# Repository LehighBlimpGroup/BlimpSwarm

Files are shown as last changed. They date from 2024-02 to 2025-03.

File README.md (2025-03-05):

# BLIMP SWARM
## [Click here for Documentation!](https://lehighblimpgroup.github.io/BlimpSwarm/)

BlimpSwarm is a framework to operate robots based on the ESP32 microcontroler.
### Please find [the indexed documentation here](https://github.com/LehighBlimpGroup/BlimpSwarm/blob/main/docs/index.md).

## FAQ

### Hardware

* Why does does only one servo or one motor not work, but the rest seem operational?
You likely have a loose/broken cable connection; If the cables are not broken (and need soldering or reinserting into the connecters), try just pushing the connectors together at every intersection. This can sometimes help the mechanical connecton to reoccur. 
If this does not solve your issue with one particular motor or servo, you might have a broken speed controller or a broken servo. Try using a test servo or test motor program to test these (or a servo tester if you have one). The motor itself can also break, and you can feel it by turining them by hand and observing the consistancy of the turning. The servo can be simalarly tested, but a servo is easier to break in this way. You can usually check if the servo is correcly powered by softly attempting to move them as they are powered and seeing if they want to move. One known issue is breaking servos due to insufficent current from the voltage booster. 

* Why does everything (motors and servos) turn on, but the robot doesnt seem to move up?
You likely have inverted motors or propellers. Make sure the propellers are correctly spinning in the correct direction and are pushing air down instead of up. If they are inverted, you need to switch any two wires in the connectors. You will need a sharp object to carefully lift the plastic blockers in the connecter to remove the wires and reinsert them in opposite positions (would recommend looking at a video).
Your robot might also be too heavy. 

* Why after I tried using all your troubleshooting tips, and I still cant solve the problem; I even used some methods you didnt mention and they failed!
There is a good chance the hardware on the PCB or the ESP32 failed. You may want to try replacing these to isolate the issue if possible to see if the issue still occurs. You may also be using an old version of the code, and may want to update the entire library to the github version. Sometimes the transeiver reduces in efficency from overuse, and the harware on the PCB can fail due to current spikes during operation. 

### Firmware

* The servos keep moving to weird positions when I start up, even though I set them to point up when the robot is in 'powered rest'. ( powered rest is the base setpoint of the servos when at rest, they should be pointing straight up).
This can be caused by the pitch feedback, try turning it off when trying. If you want pitch feedback and turining it off fixed this issue: set the pitch_offset parameter to 180 degrees from its current value. 

* Why does the flight work most of the time, but the turning while moving fowards seems very strange?
You likely have your servo1 connected to motor2 and vice versa. Check your hardware connections to make sure the front servo connection is on the same pair as the front motor connection. 

* Why does the pitch feedback fail force the servos to point straight up when it pitches, and go in the opposite direction?
Try setting inverting pitch_invert on the ground station from -1 to 1 or vice versa. 

* Why does my robot spin out of control when I start it up?
Try unplugging and replugging the blimp rapidly. Sometimes the capacitor causes the startup of the BNO to fail, and it will need a restart to correctly startup. 
Your yaw is likely inverted from the correct direction; try setting your kddyaw to negative or positive from its current direction. This is usally caused by the BNO being mounted upside down, but if that is required, you may need to edit the gains to accomidate for this. You can also double check by turining off yaw_en for yaw feedback, but your robot might unintentionally move in yaw due to the difference in servo angles when you first calibrate them. 

### Ground Station

* Why doesnt serial doesnt seem to be importing even though I did '$pip install pyserial'?: 
Your text editor is likely using a different version of python than the one you installed pyserial to: check to make sure these match or install pyserial to the installation of python used by your terminal/text editor.

* Why do I keep getting messages like "could not open port" when I run the ground station code?:
There are several reasons this could occur. 
#1 Make sure that your transiever code contains the correct 'BaseTranseiver.ino' code. 
#2 Make sure that your transiever arduino is connected to your computer, and check its port matches the one in 'user_parameters.py'.
#3 Make sure that the serial monitor of the transiever arduino is closed/not occupied by another process.

* Why isn't my blimp moving even though I turned the prorgram on?
#1 Make sure the robot is turned on.
    #a Make sure that you are sending an 'on' command in the python program (most use 'B' on the controller to start).
#2 Make sure the mac address in 'user_parameters.py' matches the mac address on the blimp.
#3 Make sure the robot code is correct: one of the bicopter.ino files ex: 'MultiRobotBicopter.ino'.
#4 Make sure the battery is charged (using a battery checker or at minimum, you hear the ESCs arm when you plug the battery in).
#5 Make sure the motors are calibrated, as the calibration might result in not seeing the motors move. 
#6 If the above fail, you can follow the following debugging procedures to isolate the issue:
#a Plug in the serial cable to the robot and observe the serial monitor:
    If the serial monitor is not printing statements that have to do with the start of a robot, or sensor measurements; you likely have the wrong firmware.
    If the serial montior is working as normal, continue.
#b Check the mac address of the robot and match it to the one in 'user_parameters.py'.
    If they are different, change and test again.
#c While observing the serial monitor, turn on the ground station code. You should see commands being recieved by the blimp on the serial monitor. (this will require two USB ports and cables) (You should not have the battery plugged into the blimp for this, unless you want to see the motors turn on while observing the serial monitor.)
    If you see nothing, you likely have some transmitter/reciever issues, but I would double check the firmware on the transeiver code, and the mac and ports are matching up on 'user_parameters.py'.
    If you see commands being recieved, you likely have a working robot, but if it still doesnt work, I would check to make sure the battery is OK and that the cables are connected correctly. Mismatches in the wiring could cause no movement even when commands are being received.

### Nicla Vision

* If you are not getting feedback from your niclavison on your arduino, you may try some of the following steps:
#1 double check that the nicla has the correct code, and it is properly downloaded on board as 'main.py'.
#2 connect the Serial monitor of your ESP32 on the blimp to the computer and make sure the nicla is powered and connected to the ESP32. Check to see if the serial monitor is getting values in the sensor measurements of the nicla (values 11-20) and that they are not crazy large values that occur when the nicla has not started up yet.
#3 double check that the nicla is properly powered, or directly connect it to your computer with a cable (will require 2 USB ports and cables)
    If you are sure that your nicla is seeing things and sending values, and you do not see anything on the ESP32 side even thought they are connected, you could have a broken Nicla vison or Nicla vision PCB. Check both by replacing them one at a time to see which is actually broken. The ESP32 PCB might also be broken but it is less likely.

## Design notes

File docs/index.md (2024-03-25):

---
title: Home
---

## BlimpSwarm Framework: Tutorials and Documentation





* [Bicopter robot: Parts and assembly](bicopter)
* [Firmware: Install and test](bicopter/firmware.md)
* [Computer Vision: Install and test](bicopter/vision.md)

More information about our team: [Swarms Lab Club](https://swarmslab.com/club/)

<iframe width="560" height="315" src="https://www.youtube.com/embed/4HuQvzdmefU?si=GS-7wAQmuWwk3HFo" title="YouTube video player" frameborder="0" allow="accelerometer; autoplay; clipboard-write; encrypted-media; gyroscope; picture-in-picture; web-share" allowfullscreen></iframe>

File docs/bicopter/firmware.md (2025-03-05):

---
title: Firmware: How to start
---

# Firmware: How to start

## 0. Before starting
Follow the instructions to assemble the robot [here](https://rhinestone-star-fa9.notion.site/Robot-Assembly-f31e5685cc46427f9f4b832dc4a56b95). Do not install the propellers.

The main board is a customized PCB that integrates the power management for the ESP32 and for the servo motors, the power outlet to the brushless ESC, the communication outlet with the vision board, and the I2C bus for the sensors.
View the PCB print of [the top layer here](https://github.com/LehighBlimpGroup/BlimpSwarm/blob/main/docs/figs/esp_board_front.pdf), and [the bottom layer here](https://github.com/LehighBlimpGroup/BlimpSwarm/blob/main/docs/figs/esp_board_back.pdf). We also provide the [Fusion 360 Electronics archive](https://github.com/LehighBlimpGroup/BlimpSwarm/blob/main/docs/figs/Blimp_ESP_board_standalone_IC_power.f3z), [the board design](https://github.com/LehighBlimpGroup/BlimpSwarm/blob/main/docs/figs/Blimp_ESP_board_standalone_IC_power.brd), [the scheme](https://github.com/LehighBlimpGroup/BlimpSwarm/blob/main/docs/figs/Blimp_ESP_board_standalone_IC_power.sch), and the [Assembly Files here](https://github.com/LehighBlimpGroup/BlimpSwarm/blob/main/docs/figs/Blimp_ESP_board_standalone_IC_power%20v94_2024-10-04.zip).

## 1. Install the robot firmware
For this part, you must have two ESP32 microchips (one with pins and one without pins). The setup looks like the following fitgure
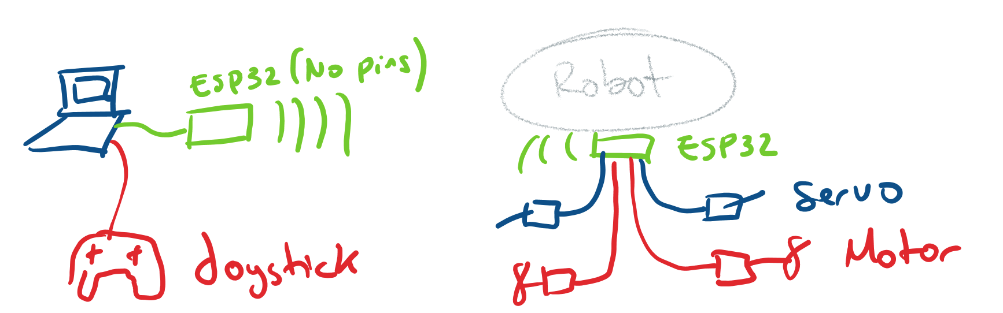
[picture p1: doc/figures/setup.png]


 Follow the following steps to install the firmware on both microchips:
1. Install [Arduino IDE 2.3.0](https://www.arduino.cc/en/software) or latest on your computer.
2. Download [BlimpSwarm](https://github.com/LehighBlimpGroup/BlimpSwarm) into the Arduino/libraries folder.
3. In Arduino open the menu ```File->Examples->BlimpSwarm->Bicopter1raw```.
4. Connect the ESP32 (with pins) to your computer through USB. 
   * Select the device XIAO_ESP32S3
   * Select the port of the ESP32. E.g., COM1 in Windows, /dev/ttyACM0 in Linux, or /dev/tty.usbmodem14301 in MacOS.
5. Click on Upload
6. Click on serial Monitor, and copy the MAC address (e.g., 34:85:18:AC:BB:70). Then, close the Serial Monitor.
7. Disconnect your ESP32 and Repeat the same process to install ```File->Examples->BlimpSwarm->BaseTranseiver``` in the ESP32 (without pinS). That is the ESP32 that will be connected to your computer and act as a radio communicator.

## 2. Control the actuators (servos and motors using the Joystick)

1. Connect the Joystick to the computer
2. Edit the Python file BlimpSwarm/swarmbase/RawBicopterJoystick.py
```
    Update the ROBOT_MAC of your robot
    Update the port of the ESP32 (same as the one in Arduino)
```
3. Run the file ```RawBicopter.py```. 
4. Move the left vertical joystick. 
   * The LED in your ESP32 should turn on when you move the vertical joystick

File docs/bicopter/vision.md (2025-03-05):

---
title: Computer Vision
---

# Vision Module

## Hardware Requirements
For this tutorial, you need the _Arduino Nicla Vision_ and the _Vision Module_.
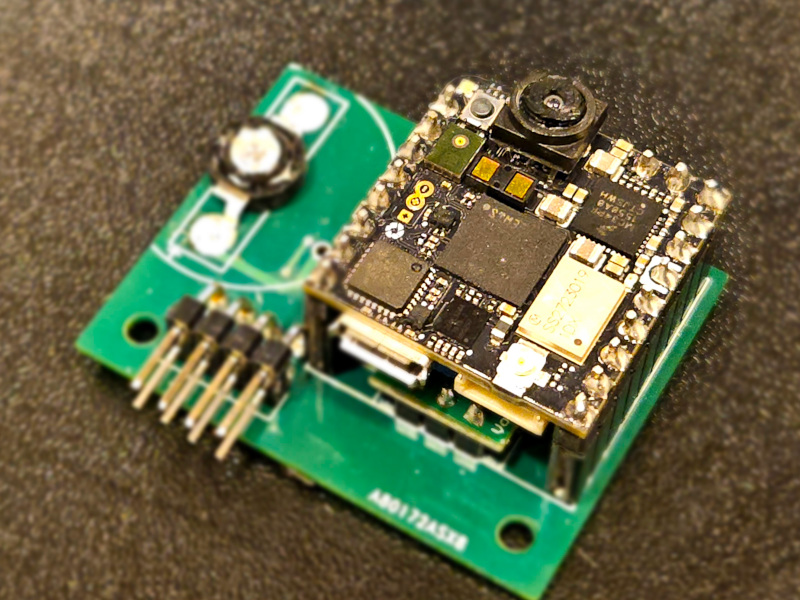
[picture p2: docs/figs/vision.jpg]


The Vision Module is a customized PCB that integrates the power management, the communication outlet with the main ESP board, and a power LED driver.
View the PCB print of [the top layer here](https://github.com/LehighBlimpGroup/BlimpSwarm/blob/main/docs/figs/nicla_board_front.pdf), and [the bottom layer here](https://github.com/LehighBlimpGroup/BlimpSwarm/blob/main/docs/figs/nicla_board_back.pdf). We also provide the [Fusion 360 Electronics archive](https://github.com/LehighBlimpGroup/BlimpSwarm/blob/main/docs/figs/Blimp_nicla_standalone_IC.f3z), [the board design](https://github.com/LehighBlimpGroup/BlimpSwarm/blob/main/docs/figs/Blimp_nicla_standalone_IC.brd), [the scheme](https://github.com/LehighBlimpGroup/BlimpSwarm/blob/main/docs/figs/Blimp_nicla_standalone_IC.sch), and the [Assembly Files here](https://github.com/LehighBlimpGroup/BlimpSwarm/blob/main/docs/figs/Blimp_nicla_standalone%20v57_2024-03-01.zip).

## Installation
1. Install _OpenMV IDE v4.1.5_ or latest from [here](https://openmv.io/pages/download)
2. Download/Clone the Gihub repository [Blob-Detection-and-Tracking](https://github.com/LehighBlimpGroup/Blob-detection-and-Tracking/blob/main/Blob%20Detection.py)

# Blob-detection-and-Tracking
Blob detection, tracking and serial communication to esp32 through IBus protocol using an OpenMV compatible edge camera device. Currently it has two modes:
1. Pure color-based blob detection and tracking, which requires a fine-tuned threshold in LAB space. Look at [OpenMV documentation on the function find_blobs](https://docs.openmv.io/library/omv.image.html#image.Image.find_blobs) for detailed reference.
2. IR blinking-based detection for retro-reflective surfaces using a IR-filter-free lens. The camera captures two consecutive images with LED off and on, respectively, then compute pixel-wise difference to highlight the reflective surfaces in the environment. Refer to [the initial tests on the reflective solution for more details](https://github.com/LehighBlimpGroup/Reflective_AimBot).
    1. Under colored mode (`isColored = True`), the algorithm distinguishes the reflective surfaces with different colors.
    2. Under grayscale mode (`isColored = False`), the algorithm does not distinguish the reflective surfaces with different colors.

Both modes use the same moving-window-based tracking methods (see classes `Tracking_ROI` and `TrackedBlob`).

## The logic flow of ROI tracking:
1. Initialize the ROI as the maximum size of the image.
2. Whenever a new detection is fed, find its bounding box.
3. New ROI is a weight average of the current rectangular ROI and the detection bounding box.

## The logic flow of the blob tracking:
1. Initialization:
    1. find a reference blob by constraining the minimum roundness, density, and of course color
    2. initialize a feature vector and a history list of blobs based on the reference
        1. *feature vector*: a vector of {five} values marking the **average** center x, y position, width, height, and blob direction of the tracked blob history
        2. *history*: a list of blobs that the algorithm considers as the same blob through multiple frames
2. Update: check the feature vector of the tracked blob against new detected blobs in terms of 1-norm/2-norm feature vector distance
    1. if the history list is full, pop the oldest, push the latest. Otherwise populate it.
    2. if the new blob feature vector is too far from the tracked blob, mark the tracked blob with an additional missed track
    3. if the tracked blob has too many missed tracks, reset the tracked blob history and feature vector, then go to step 1.ii.

## The logic flow of the retro-reflective detection:
1. IR LED off, take image1.
2. IR LED on (~2W power LEDs), take image2.
3. Compute pixel-wise difference between image1 and image2 by `diff = image2 - image1`.
4. (Optional) Filter out differences due to motion by finding high-frequency edges on image1 and use them as a `mask`.
5. Negate `diff` to recover the original color of the reflective surfaces.
6. Find colored blobs on `diff` with regions marked with `mask` masked out.

## Parameters
1. `thresholds`: it determines the color to detect and track
2. In function `find_reference`, `density_threshold` and `roundness_threshold=0.4`: they determine how strictly dense and round the initial blob needs to be.
3. In initialization of the `TrackedBlob` object currently in function `find_reference`,
    1. `norm_level` controls the distance type, 1-norm is faster and 2-norm is smoother (try both and feel the difference)
    2. `feature_dist_threshold` controls how strict a feature vector match needs to be
    3. `window_size` controls how long a history of tracked blobs the user wants to keep. Higher value gives a smoother but more draggy track
4. If the nicla is connected to another device through uart, when it receives `0x80`, it will try to switch to balloon tracking mode. When it receives `0x81`,
   it will try to switch to goal tracking mode.
5. In the initialization of `Tracking_ROI` objects, `forgetting_factor` controls how rapid the bounding box is updated with respect to a new input or a new misinput.

## Pending:
1. `id`: we would like to identify/distinguish different blobs.

## `Thresholds.txt`
We recorded the (manually-tuned) optimal color thresholds for balloon detection under different initial and ambient lighting consitions in this file.

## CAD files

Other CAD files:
docs/figs/Blimp_ESP_board_standalone_IC_power.f3z
docs/figs/Blimp_nicla_standalone_IC.f3z

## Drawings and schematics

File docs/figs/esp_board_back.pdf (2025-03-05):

I2C xZ LR | RL

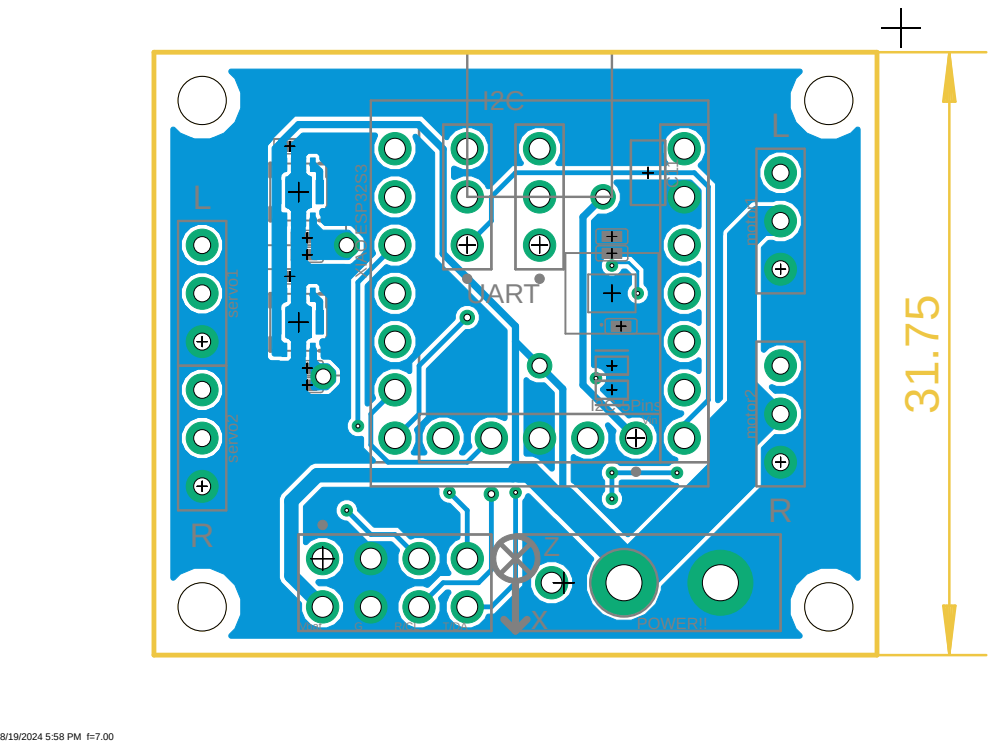
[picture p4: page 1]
Vbat; motor1 motor2 servo1 servo2; UART; I2C-5Pins; POWER!! C¹¹

Vin XIAO ESP³²S³

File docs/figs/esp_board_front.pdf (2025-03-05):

I2C
L

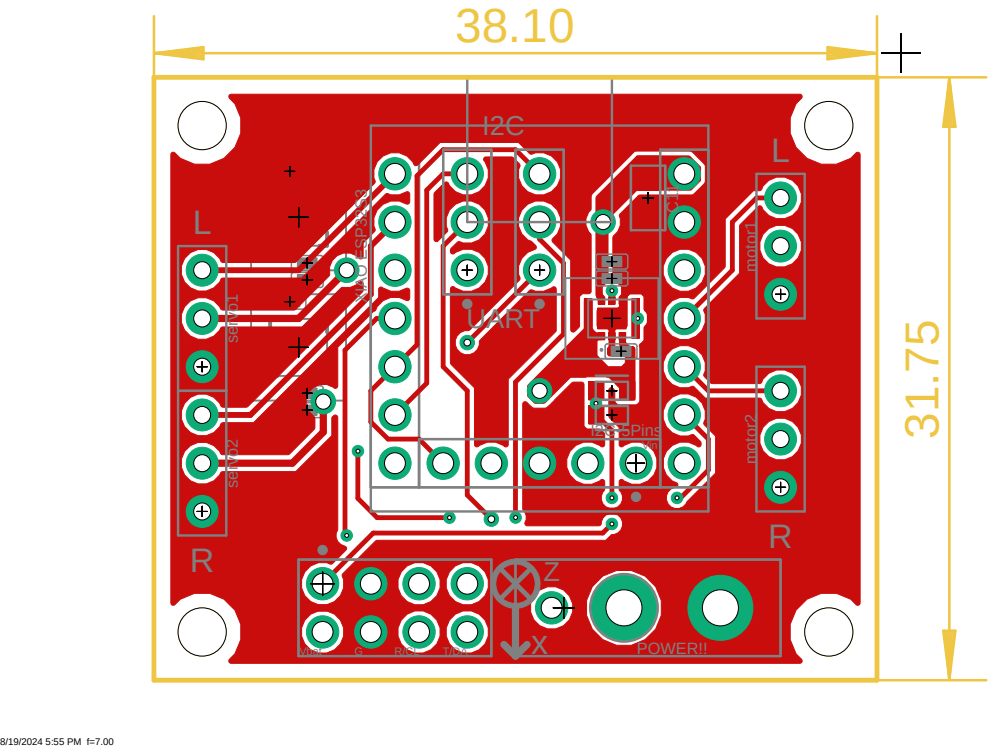
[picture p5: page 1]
Vbat; motor1 motor2 servo1 servo2; UART; I2C-5Pins; POWER!! C¹¹

Vin XIAO ESP³²S³

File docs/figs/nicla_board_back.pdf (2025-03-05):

40.64 31.75

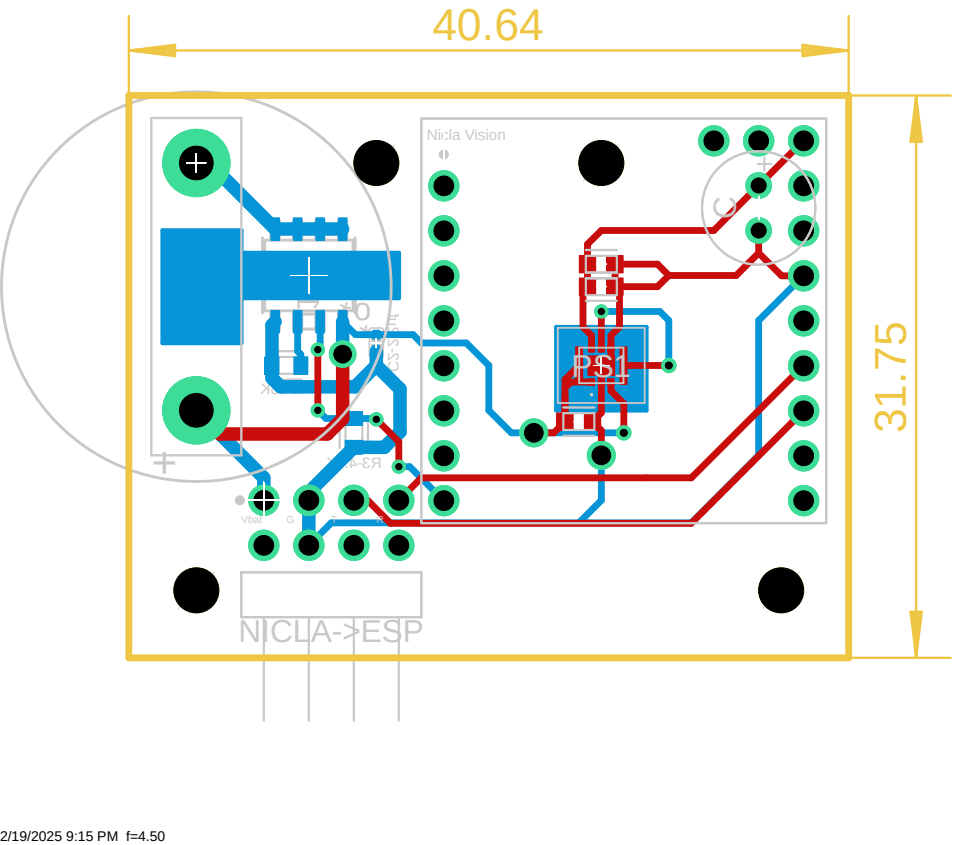
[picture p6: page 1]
Vbat; Nicla Vision; NICLA->ESP

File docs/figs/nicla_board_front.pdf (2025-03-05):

40.64 31.75

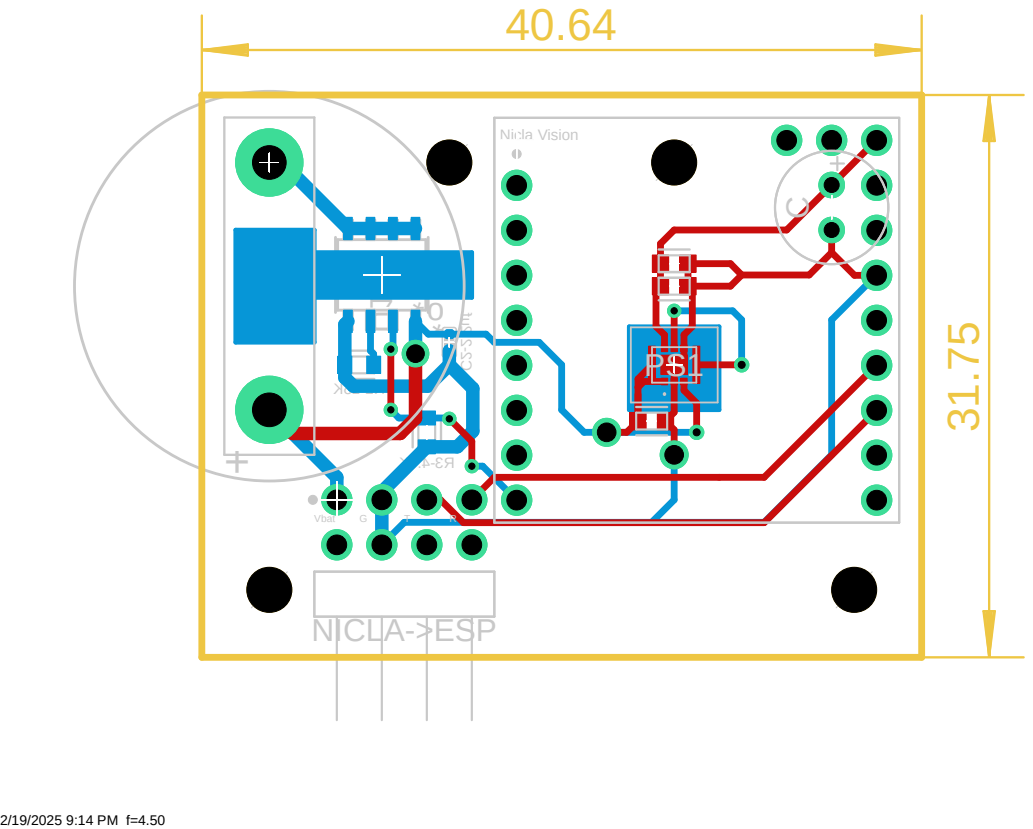
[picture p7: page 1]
Vbat; Nicla Vision; NICLA->ESP

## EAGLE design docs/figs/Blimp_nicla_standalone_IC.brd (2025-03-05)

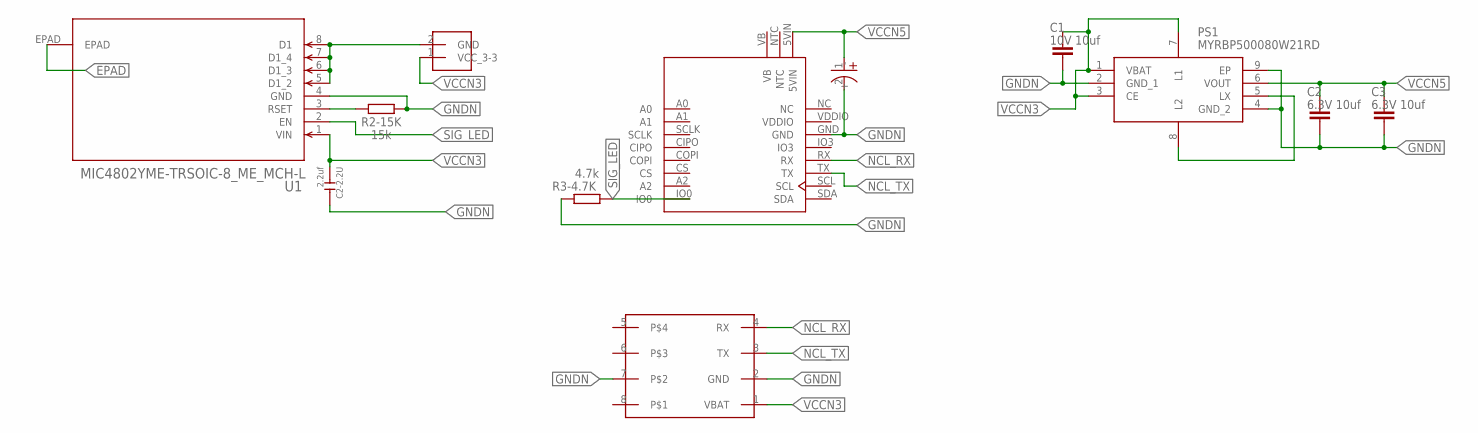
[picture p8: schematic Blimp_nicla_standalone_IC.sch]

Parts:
C1: 10V 10uf; CAPC1608X85
C2, C3: 6.3V 10uf; CAPC1608X85
C2-2.2U: 2.2uf; C0402
IR_LED1: UV_LIGHT
PS1: MYRBP500080W21RD
R2-15K: 15k; RESC1608X60
R3-4.7K: 4.7k; RESC1608X60
U1: MIC4802YME-TRSOIC-8_ME_MCH-L; SOIC-8_ME_MCH-L
U$6: NICLA_ESP_4PIN_CONNECTOR_MALE_ON_NICLA; ESP_NICLA_4X2PIN_CONNECTOR_MALE_ON_NICLA
U$9: CUSTOM_C; CAP
U$15: NICLAVISION; NICLA_FULL

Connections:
EPAD: U1.EPAD
GNDN: C1.2, C2.2, C2-2.2U.2, C3.2, PS1.2 (GND_1), PS1.4 (GND_2), PS1.9 (EP), R2-15K.2, R3-4.7K.2, U1.4 (GND), U$6.2 (GND), U$6.7, U$9.2 (-), U$15.GND
unnamed: IR_LED1.2 (GND), U1.5 (D1_2), U1.6 (D1_3), U1.7 (D1_4), U1.8 (D1)
unnamed: R2-15K.1, U1.3 (RSET)
unnamed: PS1.5 (LX), PS1.8 (L2)
NCL_RX: U$6.4 (RX), U$15.RX
NCL_TX: U$6.3 (TX), U$15.TX
SIG_LED: R3-4.7K.1, U1.2 (EN), U$15.IO0
VB: U$15.VB
VCCN3: C1.1, C2-2.2U.1, IR_LED1.1 (VCC_3-3), PS1.1 (VBAT), PS1.3 (CE), PS1.7 (L1), U1.1 (VIN), U$6.1 (VBAT)
VCCN5: C2.1, C3.1, PS1.6 (VOUT), U$9.1 (+), U$15.5VIN
VDDIO: U$15.VDDIO

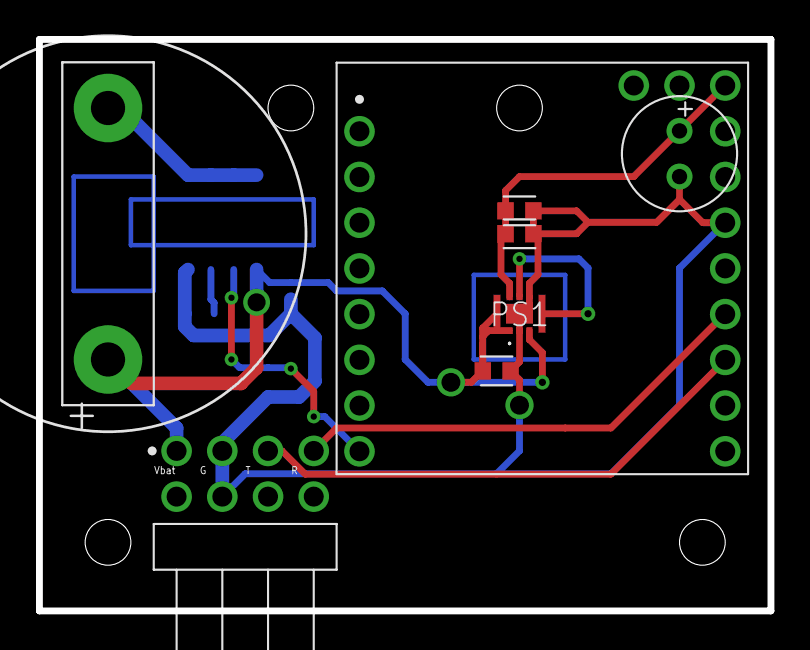
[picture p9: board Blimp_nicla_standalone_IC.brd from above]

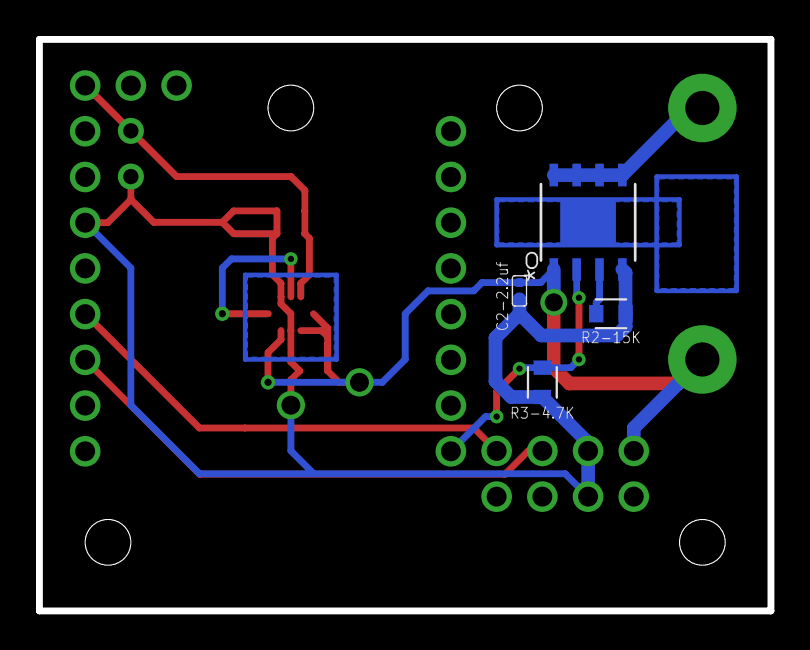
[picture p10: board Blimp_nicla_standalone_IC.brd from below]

Board: 2 copper layers, 40.6 x 31.8 mm, 12 parts (4 on the bottom side), 9 nets.

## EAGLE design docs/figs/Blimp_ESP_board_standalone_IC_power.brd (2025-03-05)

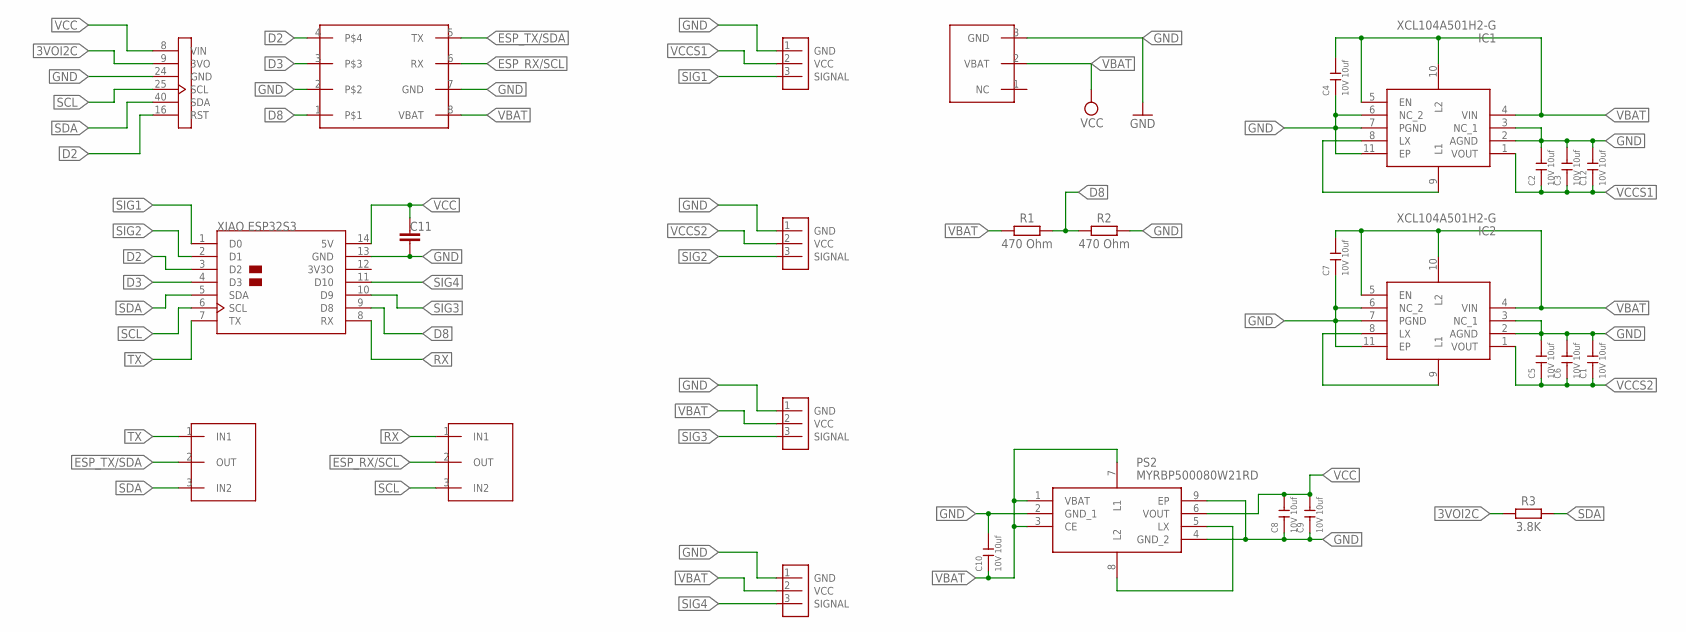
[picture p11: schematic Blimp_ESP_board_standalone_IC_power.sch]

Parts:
ACT1, ACT2, ACT3, ACT4: ESC; ESC_CONECTOR_FOOT
C1, C2, C3, C4, C5, C6, C7, C8, C9, C10, C12: 10V 10uf; C0402
C11: C_TANTALUM-1206(3216-METRIC); CAPM3216X180
IC1, IC2: XCL104A501H2-G; DFN3030-10B
PS2: MYRBP500080W21RD
R1, R2: 470 Ohm; RESC1608X60
R3: 3.8K; RESC1608X60
U1: XIAOESP32S3
U$1: BATTERY_CONNECTOR; 3PIN_CONNECTOR_FEMALE
U$2: I2C_6PIN_WRST
U$4, U$5: 3X1SELECTOR
U$7: NICLA_ESP_4PIN_CONNECTOR_FEMALE_ON_ESP; ESP_NICLA_4X2PIN_CONNECTOR_FEMALE_ON_ESP

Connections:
3VOI2C: R3.1, U$2.9 (3VO)
D2: U1.3 (D2), U$2.16 (RST), U$7.4
D3: U1.4 (D3), U$7.3
D8: R1.2, R2.1, U1.9 (D8), U$7.1
ESP_RX/SCL: U$5.2 (OUT), U$7.6 (RX)
ESP_TX/SDA: U$4.2 (OUT), U$7.5 (TX)
GND: ACT1.1 (GND), ACT2.1 (GND), ACT3.1 (GND), ACT4.1 (GND), C1.2, C2.2, C3.2, C4.1, C5.2, C6.2, C7.1, C8.1, C9.1, C10.2, C11.2, C12.2, IC1.2 (AGND), IC1.3 (NC_1), IC1.6 (NC_2), IC1.7 (PGND), IC1.11 (EP), IC2.2 (AGND), IC2.3 (NC_1), IC2.6 (NC_2), IC2.7 (PGND), IC2.11 (EP), PS2.2 (GND_1), PS2.4 (GND_2), PS2.9 (EP), R2.2, U1.13 (GND), U$1.3 (GND), U$2.24 (GND), U$7.2, U$7.7 (GND)
unnamed: IC1.8 (LX), IC1.9 (L1)
unnamed: IC2.8 (LX), IC2.9 (L1)
unnamed: PS2.5 (LX), PS2.8 (L2)
RX: U1.8 (RX), U$5.1 (IN1)
SCL: U1.6 (SCL), U$2.25 (SCL), U$5.3 (IN2)
SDA: R3.2, U1.5 (SDA), U$2.40 (SDA), U$4.3 (IN2)
SIG1: ACT3.3 (SIGNAL), U1.1 (D0)
SIG2: ACT2.3 (SIGNAL), U1.2 (D1)
SIG3: ACT1.3 (SIGNAL), U1.10 (D9)
SIG4: ACT4.3 (SIGNAL), U1.11 (D10)
TX: U1.7 (TX), U$4.1 (IN1)
VBAT: ACT1.2 (VCC), ACT4.2 (VCC), C4.2, C7.2, C10.1, IC1.4 (VIN), IC1.5 (EN), IC1.10 (L2), IC2.4 (VIN), IC2.5 (EN), IC2.10 (L2), PS2.1 (VBAT), PS2.3 (CE), PS2.7 (L1), R1.1, U$1.2 (VBAT), U$7.8 (VBAT)
VCC: C8.2, C9.2, C11.1, PS2.6 (VOUT), U1.14 (5V), U$2.8 (VIN)
VCCS1: ACT3.2 (VCC), C2.1, C3.1, C12.1, IC1.1 (VOUT)
VCCS2: ACT2.2 (VCC), C1.1, C5.1, C6.1, IC2.1 (VOUT)

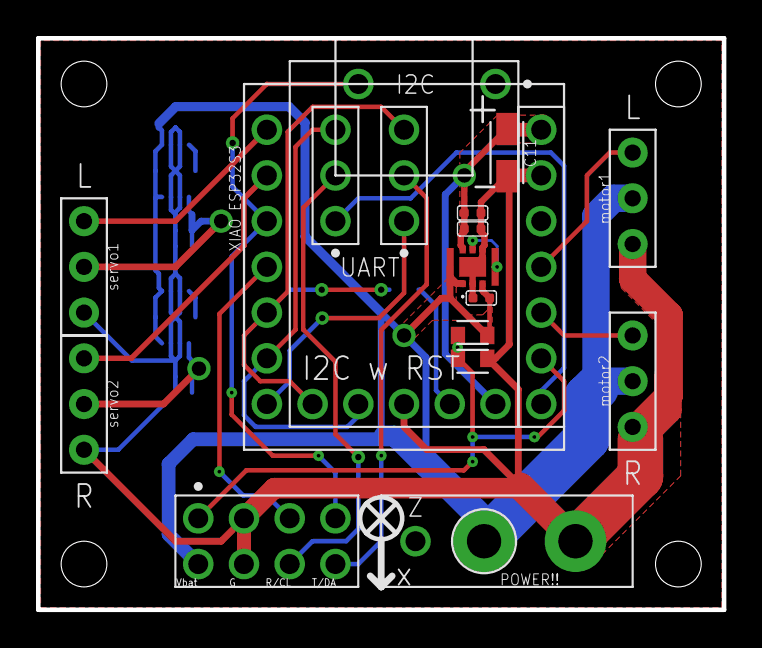
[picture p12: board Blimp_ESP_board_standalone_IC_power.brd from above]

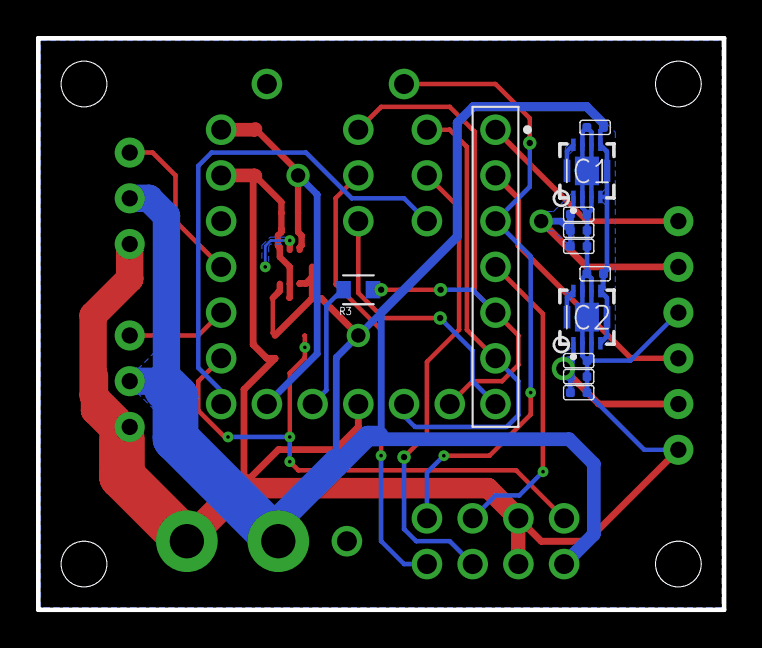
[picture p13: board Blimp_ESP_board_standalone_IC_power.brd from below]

Board: 2 copper layers, 38.1 x 31.8 mm, 28 parts (11 on the bottom side), 22 nets.

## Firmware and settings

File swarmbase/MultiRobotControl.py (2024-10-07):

import pygame
from comm.Serial import SerialController
from joystick.JoystickManager import JoystickManager
from gui.simpleGUI import SimpleGUI
from gui.niclaGUI import NiclaBox
import time
from user_parameters import ROBOT_MACS,  SERIAL_PORT, PRINT_JOYSTICK, PUMP_MAC
ROBOT_MAC = None

def main():
    serial = SerialController(SERIAL_PORT, timeout=0.5)
    if serial.serial is None:
        return
    joystick = JoystickManager()
    mygui = SimpleGUI()
    niclaGUI = NiclaBox(max_x=240, max_y=160, x=120, y=80, width=120, height=80)
    pygame.init()
    # Get all Robot Mac addresses
    robots = ROBOT_MACS
    current_robot_index = -1
    ROBOT_MAC = "00:00:00:00:00:00"#robots[current_robot_index]


    # Setup communication with robot
    for robot_mac in robots:
        serial.manage_peer("A", robot_mac)
        time.sleep(0.05)
    # Setup communication with pump
    serial.manage_peer("A", PUMP_MAC)
    
    sensors = serial.getSensorData()
    # Initialize control variables
    height, tz =  (0, 0)
    ready = [0] * len(robots)
    old_buttons = [0] * 4  # A, B, X, Y
    fx_ave = 0
    dt = 0.3
    pump = False
    

    try:
        running = True
        while running:
            for event in pygame.event.get():
                if event.type == pygame.KEYDOWN: # If a keyboard button is pressed
                    if event.key == pygame.K_PERIOD:
                        print("Pump On")
                        serial.send_control_params(PUMP_MAC, (1, 0, 0, 0, 0, 250, 0, 0, 0, 0, 0, 0, 0))
                    elif event.key == pygame.K_COMMA:
                        print("Pump Off")
                        serial.send_control_params(PUMP_MAC, (0, 0, 0, 0, 0, 0, 0, 0, 0, 0, 0, 0, 0))
                    elif event.key == pygame.K_m:
                        serial.send_control_params(robots[4], (1, 0, 5, 0, 0, 0, 0, 0, 0, 0, 0, 0, 0))
                    elif event.key == pygame.K_k:
                        serial.send_control_params(robots[2], (1, 0, 4, 0, 0, 0, 0, 0, 0, 0, 0, 0, 0))

                    # QWERTY row for setting flag 2
                    elif event.key == pygame.K_q: # Flag 2 to blimp 0
                        serial.send_control_params(robots[0], (3, 0, 0, 0, 0, 0, 0, 0, 0, 0, 0, 0, 0))
                        time.sleep(.1)
                        serial.send_control_params(robots[0], (2, 0, 0, 0, 0, 0, 0, 0, 0, 0, 0, 0, 0))
                    elif event.key == pygame.K_w: # Flag 2 to blimp 1
                        serial.send_control_params(robots[1], (3, 0, 0, 0, 0, 0, 0, 0, 0, 0, 0, 0, 0))
                        time.sleep(.1)
                        serial.send_control_params(robots[1], (2, 0, 0, 0, 0, 0, 0, 0, 0, 0, 0, 0, 0))
                    elif event.key == pygame.K_e: # Flag 2 to blimp 2
                        serial.send_control_params(robots[2], (3, 0, 0, 0, 0, 0, 0, 0, 0, 0, 0, 0, 0))
                        time.sleep(.1)
                        serial.send_control_params(robots[2], (2, 0, 0, 0, 0, 0, 0, 0, 0, 0, 0, 0, 0))
                    elif event.key == pygame.K_r: # Flag 2 to blimp 3
                        serial.send_control_params(robots[3], (3, 0, 0, 0, 0, 0, 0, 0, 0, 0, 0, 0, 0))
                        time.sleep(.1)
                        serial.send_control_params(robots[3], (2, 0, 0, 0, 0, 0, 0, 0, 0, 0, 0, 0, 0))
                    elif event.key == pygame.K_t: # Flag 2 to blimp 4
                        serial.send_control_params(robots[4], (3, 0, 0, 0, 0, 0, 0, 0, 0, 0, 0, 0, 0))
                        time.sleep(.1)
                        serial.send_control_params(robots[4], (2, 0, 0, 0, 0, 0, 0, 0, 0, 0, 0, 0, 0))
                    elif event.key == pygame.K_y: # Flag 2 to blimp 5
                        serial.send_control_params(robots[5], (3, 0, 0, 0, 0, 0, 0, 0, 0, 0, 0, 0, 0))
                        time.sleep(.1)
                        serial.send_control_params(robots[5], (2, 0, 0, 0, 0, 0, 0, 0, 0, 0, 0, 0, 0))

                    # ASDFGH row for setting flag 0
                    elif event.key == pygame.K_a: # Flag 3 to blimp 0
                        serial.send_control_params(robots[0], (0, 0, 0, 0, 0, 0, 0, 0, 0, 0, 0, 0, 0))
                    elif event.key == pygame.K_s: # Flag 3 to blimp 1
                        serial.send_control_params(robots[1], (0, 0, 0, 0, 0, 0, 0, 0, 0, 0, 0, 0, 0))
                    elif event.key == pygame.K_d: # Flag 3 to blimp 2
                        serial.send_control_params(robots[2], (0, 0, 0, 0, 0, 0, 0, 0, 0, 0, 0, 0, 0))
                    elif event.key == pygame.K_f: # Flag 3 to blimp 3
                        serial.send_control_params(robots[3], (0, 0, 0, 0, 0, 0, 0, 0, 0, 0, 0, 0, 0))
                    elif event.key == pygame.K_g: # Flag 3 to blimp 4
                        serial.send_control_params(robots[4], (0, 0, 0, 0, 0, 0, 0, 0, 0, 0, 0, 0, 0))
                    elif event.key == pygame.K_h: # Flag 3 to blimp 5
                        serial.send_control_params(robots[5], (0, 0, 0, 0, 0, 0, 0, 0, 0, 0, 0, 0, 0))

                    # ZXCVB row for setting flag 4
                    elif event.key == pygame.K_z: # Flag 4 to blimp 0
                        serial.send_control_params(robots[0], (4, 0, 0, 0, 0, 0, 0, 0, 0, 0, 0, 0, 0))
                    elif event.key == pygame.K_x: # Flag 4 to blimp 1
                        serial.send_control_params(robots[1], (4, 0, 0, 0, 0, 0, 0, 0, 0, 0, 0, 0, 0))
                    elif event.key == pygame.K_c: # Flag 4 to blimp 2
                        serial.send_control_params(robots[2], (4, 0, 0, 0, 0, 0, 0, 0, 0, 0, 0, 0, 0))
                    elif event.key == pygame.K_v: # Flag 4 to blimp 3
                        serial.send_control_params(robots[3], (4, 0, 0, 0, 0, 0, 0, 0, 0, 0, 0, 0, 0))
                    elif event.key == pygame.K_b: # Flag 4 to blimp 4
                        serial.send_control_params(robots[4], (4, 0, 0, 0, 0, 0, 0, 0, 0, 0, 0, 0, 0))

                    if event.key == pygame.K_SPACE:
                        for robot_mac in robots:
                            serial.send_control_params(robot_mac, (3, 0, 0, 0, 0, 0, 0, 0, 0, 0, 0, 0, 0))
                            time.sleep(.2)
                            serial.send_control_params(robot_mac, (2, 0, 0, 0, 0, 0, 0, 0, 0, 0, 0, 0, 0))
                            time.sleep(.1)
                        ready[current_robot_index] = 2
                    elif event.key == pygame.K_p:
                        count = 0
                        for robot_mac in robots:
                            ready[count] = 0
                            count += 1
                            serial.send_control_params(robot_mac, (0, 0, 0, 0, 0, 0, 0, 0, 0, 0, 0, 0, 0))
                            time.sleep(.1)
                        ready[current_robot_index] = 0
                        
                    elif event.key == pygame.K_o:
                        
                        for robot_mac in robots[:-2]:
                            serial.send_control_params(robot_mac, (4, 0, 0, 0, 0, 0, 0, 0, 0, 0, 0, 0, 0))
                            time.sleep(.1)
                            
                    elif event.key == pygame.K_i:
                        count = 0
                        for robot_mac in robots:
                            ready[count] = 3
                            count+=1
                            serial.send_control_params(robot_mac, (3, 0, 2, 0, 0, 0, 0, 0, 0, 0, 0, 0, 0))
                            time.sleep(.1)
                    elif event.key == pygame.K_u:
                        for robot_mac in robots[:-2]:
                            serial.send_control_params(robot_mac, (2, 0, 0, 0, 0, 0, 0, 0, 0, 0, 0, 0, 0))
                            time.sleep(.1)       
                    elif event.key == pygame.K_ESCAPE:
                        running = False
                    elif pygame.K_0 <= event.key <= pygame.K_9:
                        index = event.key - pygame.K_0 - 1
                        if 0 <= index < len(robots):
                            if current_robot_index == index:
                                print("Already set to that robot.")
                            else:
                                serial.send_control_params(ROBOT_MAC, (5, fx_ave, height, 0, tz, 0, 0, 0, 0, 0, 0, 0, 0))
                                serial.send_control_params(ROBOT_MAC, (ready[current_robot_index], fx_ave, height, 0, tz, 0, 0, 0, 0, 0, 0, 0, 0))
                                current_robot_index = index
                                ROBOT_MAC = robots[current_robot_index]
                                serial.send_control_params(ROBOT_MAC, (5, 0, 0, 0, 0, 0, 1, 0, 0, 0, 0, 0, 0))
                                time.sleep(0.1)
                                sensors = serial.getSensorData()
                                if sensors is None:
                                    height, tz = 0, 0
                                else:
                                    height, tz = (sensors[0], sensors[1])
                                
                                print(f"Switched to robot {ROBOT_MAC}")
                        else:
                            serial.send_control_params(ROBOT_MAC, (5, fx_ave, height, 0, tz, 0, 0, 0, 0, 0, 0, 0, 0))
                            current_robot_index = index
                            ROBOT_MAC = "00:00:00:00:00:00"
            axis, buttons = joystick.getJoystickInputs()

            sensors = serial.getSensorData()
            if sensors:
                s = ''
                for senses in sensors:
                    s += str(senses) + ' '
                print(s)
                if sensors[2] < 300:
                    niclaGUI.update(x=sensors[2], y=sensors[3], width=sensors[4], height=sensors[4])
                mygui.update(cur_yaw=sensors[1], des_yaw=tz, cur_height=sensors[0], des_height=height,
                             battery=sensors[5], distance=0, connection_status=True)
            
            # Button press logic
            if buttons[3] and not old_buttons[3]:  # Y puts into goal mode
                ready[current_robot_index] = 4 #if ready != 3 else 4
            if buttons[1] and not old_buttons[1]:  # B toggles pause
                ready[current_robot_index] = 0 if ready[current_robot_index] else 1
                if sensors:
                    height, tz = (sensors[0], sensors[1])
            if buttons[2] and not old_buttons[2]:  # X puts into ball mode
                ready[current_robot_index] = 3
                height, tz = (sensors[0], sensors[1])
            if buttons[0] and not old_buttons[0]:  # A sets specific ready state
                ready[current_robot_index] = 2

            # Update old button states
            old_buttons = buttons[:]
            
            # Display joystick values if enabled
            if PRINT_JOYSTICK:
                print(" ".join(["{:.1f}".format(num) for num in axis]), buttons)

            if ready[current_robot_index] != 5:
                # Control inputs to the robot
                height += -axis[0] * dt if abs(axis[0]) >= 0.15 else 0
                height = max(min(height, 15), -10)
                tz += -axis[4] * 1.2 * dt if abs(axis[4]) >= 0.15 else 0
            else:
                # Control inputs to the robot
                height = -axis[0] * .5 * dt if abs(axis[0]) >= 0.15 else 0
                tz = -axis[4] * .5 * dt if abs(axis[4]) >= 0.15 else 0
            fx_ave = (-axis[2] + axis[5]) * 0.65
            # fx_ave = fx_ave * 0.67 + fx * 0.33

            # send control parameters
            serial.send_control_params(ROBOT_MAC, (ready[current_robot_index], fx_ave, height, 0, tz, -buttons[2], 1, 0, 0, 0, 0, 0, 0))
            
            time.sleep(dt)
    except KeyboardInterrupt:
        print("Stopping!")
    finally:
        serial.send_control_params(ROBOT_MAC, (5, 0, 0, 0, 0, 0, 0, 0, 0, 0, 0, 0, 0))
        for robot_mac in robots:
            serial.send_control_params(robot_mac, (0, 0, 0, 0, 0, 0, 0, 0, 0, 0, 0, 0, 0))
            time.sleep(0.05)
        serial.send_control_params(PUMP_MAC, (0, 0, 0, 0, 0, 0, 0, 0, 0, 0, 0, 0, 0))
        time.sleep(0.05)

if __name__ == "__main__":
    main()

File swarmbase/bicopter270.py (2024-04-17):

from comm.Serial import SerialController, DataType_Int, DataType_Float, DataType_Boolean
from joystick.JoystickManager import JoystickManager
from gui.simpleGUI import SimpleGUI
from gui.niclaGUI import NiclaBox
import time

##### Insert your robot's MAC ADDRESS here ####
## (you can get it by running your arduino and looking at the serial monitor for your flying drone) ##
ROBOT_MAC = "34:85:18:AC:0E:30"#"34:85:18:AB:FE:68" # "DC:54:75:D7:B3:E8"
PASSIVE_ROBOT_MAC = "48:27:E2:E6:E0:1C"#48:27:E2:E6:E0:1C
### Insert your SERIAL PORT here ###
## may look like "COM5" in windows or "/dev/tty.usbmodem14301" in mac  #
## look in arduino for the port that your specific transeiver is connected to  ##
## Note: make sure that your serial monitor is OFF in arduino or else you will get "access is denied" error. ##
PORT = "COM12"


# For debug purposes
PRINT_JOYSTICK = False


BaseStationAddress = "" # you do not need this, just make sure your DroneMacAddress is not your base station mac address

def sendParamsActive(serial, mac):
    serial.manage_peer("A", mac)
    time.sleep(.05)
    serial.send_preference(mac, DataType_Boolean, "zEn", True)
    serial.send_preference(mac, DataType_Boolean, "rollEn", False)
    serial.send_preference(mac, DataType_Boolean, "rotateEn", False)
    serial.send_preference(mac, DataType_Boolean, "pitchEn", True)
    serial.send_preference(mac, DataType_Boolean, "yawEn", True)


    # // PID terms
    serial.send_preference(mac, DataType_Float, "kpyaw", .8) #2
    serial.send_preference(mac, DataType_Float, "kdyaw", 1.1)#.1
    serial.send_preference(mac, DataType_Float, "kiyaw", 0)
    serial.send_preference(mac, DataType_Float, "kiyawrate", 0)

    serial.send_preference(mac, DataType_Float, "kpz", 0.3)
    serial.send_preference(mac, DataType_Float, "kdz", 0.6)
    serial.send_preference(mac, DataType_Float, "kiz", 0.1)
    serial.send_preference(mac, DataType_Float, "kproll", 0)
    serial.send_preference(mac, DataType_Float, "kdroll", 0)

    # // Range terms for the integrals

    serial.send_preference(mac, DataType_Float, "z_int_low", 0.05)
    serial.send_preference(mac, DataType_Float, "z_int_high", 0.15)
    serial.send_preference(mac, DataType_Float, "yawRateIntRange", 0)

    # // radius of the blimp
    serial.send_preference(mac, DataType_Float, "lx", 0.7)
    serial.send_preference(mac, DataType_Float, "servoRange", 260) #degrees
    serial.send_preference(mac, DataType_Float, "servoBeta", 90) #degrees
    serial.send_preference(mac, DataType_Float, "botZlim", -1)
    serial.send_preference(mac, DataType_Float, "pitchOffset", 0) #degrees
    serial.send_preference(mac, DataType_Float, "pitchInvert", -1) #degrees
    serial.send_control_params(mac, (0,0,0,0, 0, 0, 0, 0, 0, 0, 0, 1, 0))
    time.sleep(.2)

def sendParamsPassive(serial, mac):
    serial.manage_peer("A", mac)
    time.sleep(.05)
    serial.send_preference(mac, DataType_Boolean, "zEn", False)
    serial.send_preference(mac, DataType_Boolean, "rollEn", False)
    serial.send_preference(mac, DataType_Boolean, "rotateEn", False)
    serial.send_preference(mac, DataType_Boolean, "pitchEn", False)
    serial.send_preference(mac, DataType_Boolean, "yawEn", False)


    # // PID terms
    serial.send_preference(mac, DataType_Float, "kpyaw", 1.5) #2
    serial.send_preference(mac, DataType_Float, "kdyaw", .1)#.1
    serial.send_preference(mac, DataType_Float, "kiyaw", 0)
    serial.send_preference(mac, DataType_Float, "kiyawrate", 0)

    serial.send_preference(mac, DataType_Float, "kpz", 0.3)
    serial.send_preference(mac, DataType_Float, "kdz", 0.6)
    serial.send_preference(mac, DataType_Float, "kiz", 0.1)
    serial.send_preference(mac, DataType_Float, "kproll", 0)
    serial.send_preference(mac, DataType_Float, "kdroll", 0)

    # // Range terms for the integrals

    serial.send_preference(mac, DataType_Float, "z_int_low", 0.05)
    serial.send_preference(mac, DataType_Float, "z_int_high", 0.15)
    serial.send_preference(mac, DataType_Float, "yawRateIntRange", 0)

    # // radius of the blimp
    serial.send_preference(mac, DataType_Float, "lx", 0.7)
    serial.send_preference(mac, DataType_Float, "servoRange", 180) #degrees
    serial.send_preference(mac, DataType_Float, "servoBeta", 45) #degrees
    serial.send_preference(mac, DataType_Float, "botZlim", -1)
    serial.send_preference(mac, DataType_Float, "pitchOffset", 0) #degrees
    serial.send_preference(mac, DataType_Float, "pitchInvert", -1) #degrees
    serial.send_control_params(mac, (0,0,0,0, 0, 0, 0, 0, 0, 0, 0, 1, 0))
    time.sleep(.2)


if __name__ == "__main__":
    # Communication
    serial = SerialController(PORT, timeout=.5)  # 5-second timeout
    serial.manage_peer("G", ROBOT_MAC)
    sendParamsActive(serial, ROBOT_MAC)
    sendParamsPassive(serial, PASSIVE_ROBOT_MAC)

    sensors = serial.getSensorData()
    height = 0
    tz = 0
    if (sensors) :
        tz = sensors[1]
        height = sensors[0]
    # Joystick
    joystick = JoystickManager()
    mygui = SimpleGUI()
    niclaGUI = NiclaBox(max_x=240, max_y=160, x=120, y=80, width=120, height=80)
    ready = 0
    old_b = 0
    old_x = 0
    dt = .1
    servos = 75
    fz2 = 0
    fx2 = .3
    try:
        while True:
            # Axis input: [left_vert, left_horz, right_vert, right_horz, left_trigger, right_trigger]
            # Button inputs: [A, B, X, Y]
            axis, buttons = joystick.getJoystickInputs()

            if buttons[3] == 1: # y stops the program
                break
            if buttons[1] == 1 and old_b == 0: # b pauses the control
                if ready != 0:
                    ready = 0
                else:
                    ready = 1
            if buttons[2] == 1 and old_x == 0:
                if fz2 <= 0:
                    fz2 = -.4
                    fx2 = .5
                else:
                    fz2 = 0
                    fx2 = .3

            old_x = buttons[2]
            old_b = buttons[1]
            if PRINT_JOYSTICK:
                print(" ".join(["{:.1f}".format(num) for num in axis]), buttons)

            #### CONTROL INPUTS to the robot here #########
            if abs(axis[0]) < .15:
                axis[0] = 0
            height += -axis[0] * dt
            if height > 15:
                height = 15
            elif height < -5:
                height = -5
            # fz2 = -axis[0] * .4

            if abs(axis[1]) < .15:
                axis[1] = 0
            tx = axis[1] * .5

            if abs(axis[4]) < .15:
                axis[4] = 0
            tz += -axis[4] *2.2 * dt
            tz2 = -axis[4] * .1

            fx = axis[2] - axis[5]
            if (fx < 0):
                fx = fx * .3

            #print(tz, ":", height)
            #print(height)
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

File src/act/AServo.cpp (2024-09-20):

/**
 * @file AServo.cpp
 * @author David Saldana
 * @brief Implementation of Aservo.h
 * @version 0.1
 * @date 2024-02-09
 * 
 * @copyright Copyright (c) 2024
 * 
 */

#include "AServo.h"



AServo::AServo(int minVal, int maxVal, int offsetVal, int pinVal, int periodHertz): Actuator(minVal, maxVal, offsetVal, pinVal) {
    // Additional initialization specific to servos
    this->period_hertz = periodHertz;
    pinMode(this->pin, OUTPUT);
    servo.attach(this->pin, this->min, this->max);
    servo.setPeriodHertz(this->period_hertz);
}

AServo::AServo(int pinVal): Actuator(550, 2450, 0, pinVal) {
    // Additional initialization specific to servos
    pinMode(this->pin, OUTPUT);
    servo.attach(this->pin, this->min, this->max);
    servo.setPeriodHertz(50); // Standard 50hz servo
}


void AServo::act(float value){
    //TODO the input should be force. We should use the calibration parameters
    //TODO the thrust is related to angular velocity
    int angle = constrain(value, 0, 180) ; // cant handle values between PI and 2PI
    servo.write((int) angle);
//    int val = constrain(value, 0, 1);
//    this->thrust.writeMicroseconds((int)((val) * (this->max - this->min) + this->min));
}

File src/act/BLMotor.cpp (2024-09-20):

/**
 * @file BLMotor.cpp
 * @author David Saldana
 * @brief Implementation of BLMotor.h
 * @version 0.1
 * @date 2024-02-09
 * 
 * @copyright Copyright (c) 2024
 * 
 */

#include "BLMotor.h"
#include <Arduino.h>



BLMotor::BLMotor(int minVal, int maxVal, int offsetVal, int pinVal, int periodHertz)
        : Actuator(minVal, maxVal, offsetVal, pinVal) {
    // Additional initialization specific to SpecificActuator
    this->period_hertz = periodHertz;
    pinMode(this->pin, OUTPUT);

    this->thrust.attach(this->pin, this->min, this->max);
    this->thrust.setPeriodHertz(this->period_hertz);
}

BLMotor::BLMotor(int pinVal)
        : Actuator(1100, 2000, 0, pinVal) {
    // Additional initialization specific to SpecificActuator
    pinMode(pinVal, OUTPUT);
    this->thrust.attach(this->pin, this->min, this->max);
    this->thrust.setPeriodHertz(50);
}


void BLMotor::act(float value){
    value = constrain(value, 0, 1);

    // Force to PWM
    float force = value * (max_thrust - min_thrust) + min_thrust;
    int pwm = (int) ((force - pwm_b) / pwm_a);
    this->thrust.writeMicroseconds(pwm);
}



void BLMotor::calibrate(){

    delay(1000);
    Serial.println("Calibrating ESCs....");
    thrust.writeMicroseconds(this->max);
    delay(8000);

    // Back to minimum value
    thrust.writeMicroseconds(this->min);
    delay(8000);
    thrust.writeMicroseconds(0);
    delay(1000);
    Serial.println("Calibration completed");
}


void BLMotor::arm(){
// ESC arming sequence for BLHeli S
    thrust.writeMicroseconds(this->min);
    delay(10);

    // Sweep up
    for (int i = 1050; i < 1500; i++)
    {
        thrust.writeMicroseconds(i);
        delay(6);
    }

    thrust.writeMicroseconds(1000);
    delay(1000);
}

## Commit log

2024-02-02 Ground Station Params Test
2024-02-06 bugfix of float_min issue
    [ParameterMessage.cpp, RawBicopter.cpp]
2024-02-06 ground station interface
2024-02-08 control LED with left joystick
2024-02-10 modularizing code for actuators
2024-02-10 battery sensor and communication is simpler.
2024-02-16 Calibration Working
2024-02-21 - pwm to force conversion in BLMotor - Calibration in RawBicopter
2024-02-22 Bug fix in motors
    Motor documentation
    [motor_profile.xlsx]
2024-02-22 Ground Station Barometer Access
2024-03-01 Sensors in new framework working; test using TestSensors.ino
2024-03-02 Better visualization for initialization on sensors
2024-03-06 adding assembly documentation
2024-03-08 Increased ease of use for sensors
2024-03-08 Ease of use change for interfacing with sensors
2024-03-11 BNO085 retry timer implementation
2024-03-14 Minor fixes in sensor rates
    [BNO85.cpp, Barometer390.cpp]
2024-03-14 Pitch inversion from ground station
2024-03-18 Moving storage of ground height for consistancy.
2024-03-18 Prototype single-behavior for goal scoring
2024-03-19 270 servo bugfixes
2024-03-25 - user parameters are in a different file - Yaw Bicopter includes manual input
2024-03-25 270 servo bicopter
2024-03-26 better gyro/accel from BNO
2024-03-28 yaw adjustments for tuning
2024-03-28 preferences added to sensors
2024-04-07 BNO sensor startup bugfix
    [BNO85.cpp, BNO85.h, Barometer.cpp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]
2024-04-09 Reel and roll/pitch
2024-04-10 Setting midpoint on continuous servo
2024-04-11 Nicla yaw enabled controller
2024-04-12 Modifications for camera and LED
2024-04-12 bugfix for non-specific application
    [Nicla.cpp]
2024-04-17 battery changes
2024-04-18 Switching goal and balloon
2024-04-18 nicla vision with balloon detection and charge for 3 seconds once some criteria is satisfied - currently shifts state to levy walk after a charge
2024-04-18 nicla vision with balloon detection and charge for 3 seconds once some criteria is satisfied - fixed a bug wrt the positive detection edge
2024-04-18 yaw bugfix
2024-04-23 Arming sequence before sensors
2024-04-23 The charge in balloon mode is constrained with centered balloon
2024-04-24 Pump refinement
2024-07-24 Fix issue with manual state transition and change charge behavior
    [BaseCommunicator.cpp, FullBicopter.cpp, MultiRobotControl.py]
2024-08-15 Fix issue with PDTerms
    [LevyWalk.cpp, MultiRobotControl.py]
2024-10-23 optimised differential control on yaw and hover behavior
2024-11-02 Wall detection and avoidance using ultrasonic sensor
    1. Ultrasonic sensor included in sensor suite
    2. Wall detection and avoidance incorporated in Levywalk
    [LevyWalk.cpp]
2024-11-06 Minor changes to main-ultrasonic branch after testing them in differential-ultrasonic Works fine in the absence of vison module
2024-11-06 Fix bug with nicla pursuit
    [LevyWalk.cpp]
2024-11-08 levy walk code, preferences to lower case
2024-11-18 no yaw on goal charge, minimum height enforced during moveToGoal
2024-11-21 fix levywalk and initial charge forward
    [LevyWalk.cpp]
2024-11-21 add color switch
2025-03-17 Levy spiral using yaw instead of time
2025-04-18 fix ultrasonic
2025-04-19 fix levy walk and preferences
    [Differential.cpp, LevyWalk.cpp]
2025-09-17 remove unnecessary artifacts
    [Blimp_ESP_board_standalone_IC_power.brd, Blimp_ESP_board_standalone_IC_power.f3z, Blimp_ESP_board_standalone_IC_power.sch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]
2025-12-03 copy doc folder for the githubpage from agile blimp to main
    [Blimp_ESP_board_standalone_IC_power.brd, Blimp_ESP_board_standalone_IC_power.f3z, Blimp_ESP_board_standalone_IC_power.sch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]
2025-12-03 get rid of duplicate
    [Blimp_ESP_board_standalone_IC_power.brd, Blimp_ESP_board_standalone_IC_power.f3z, Blimp_ESP_board_standalone_IC_power.sch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]

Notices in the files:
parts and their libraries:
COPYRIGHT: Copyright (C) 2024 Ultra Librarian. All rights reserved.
